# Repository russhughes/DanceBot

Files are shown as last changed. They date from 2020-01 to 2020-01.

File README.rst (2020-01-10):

DanceBot
========

This is my adaptation of the Bobwi DanceBot (https://github.com/G4lile0/Bobwi)
inspired by Zowi (http://diwo.bq.com/en/zowi-cc-by-sa/) and is licesed the same
the originals Attribution-ShareAlike 4.0 International (CC BY-SA 4.0)
http://creativecommons.org/licenses/by-sa/4.0/

|

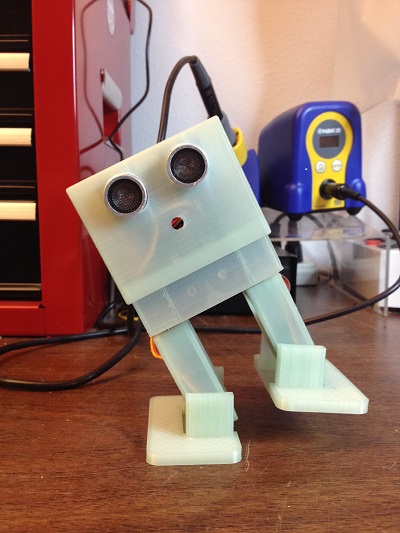
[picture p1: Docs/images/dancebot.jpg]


|

My goal was to simplify assembly for use in Workshops at my local Makerspace
https://confluent.space/. A custom PC board using an Arduino Pro Mini or 
compatible was created to make the electronics assembly easier as well.

|

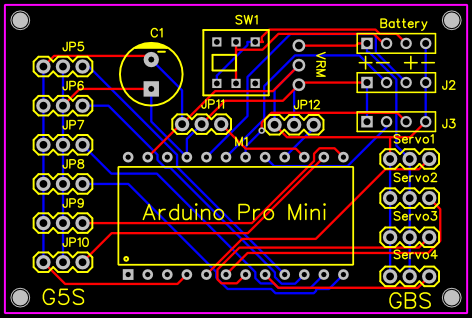
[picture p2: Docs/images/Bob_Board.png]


|

The build instuctions are almost complete but they could use a bit more editing
and a section on calibration.

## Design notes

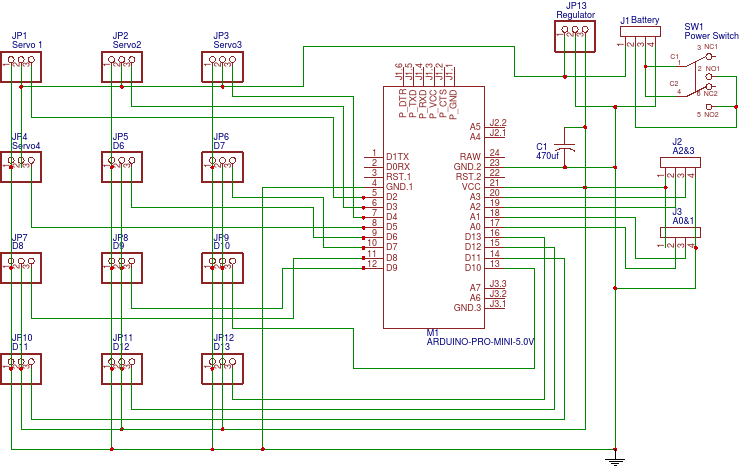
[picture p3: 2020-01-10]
Docs/images/Bob Board Schematic.png

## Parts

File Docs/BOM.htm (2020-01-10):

Dancebot Parts List
1 | 3D Printed parts
1 | Arduino Pro Mini | https://smile.amazon.com/gp/product/B015MGHLNA/
4 | MG90s Servo | https://smile.amazon.com/gp/product/B006VRWV1W/
4 | AA Battery | Almost Anywhere
1 | HC-SR04 | https://smile.amazon.com/gp/product/B00P5W1JLM
1 | 8x8 mm Self-Locking Push Button | https://www.amazon.com/dp/B009750CS4/
2 | 2 x AA 1.5V Battery Holder | https://smile.amazon.com/gp/product/B013GNC08C
1 | CP2102 USB-TTL Board or Similar | https://smile.amazon.com/gp/product/B00SL0U3RG
1 | Pololu #2119 5V Step-up/step-down | https://www.pololu.com/product/2119
1 | DanceBot PCB | https://easyeda.com/EZG0bble/New_Project-Dlf93lfwO
1 | 470uF Electrolytic Capacitor | https://smile.amazon.com/gp/product/B0063C0MPC
2 | 12 Pin Female Header | https://smile.amazon.com/gp/product/B00TGOJE1W
1 | 3 Pin Female Header | "
1 | 6 Pin Male Header | https://smile.amazon.com/gp/product/B00R1LEIL8
2 | 4 Pin Male Header | "
4 | 3 Pin Male Header | "
4 | 2-56 x 3/8" Philips Machine Screw | https://smile.amazon.com/gp/product/B00GX0978W
4 | 2-56 x 1/4" Philips Self Tap Screw | https://smile.amazon.com/gp/product/B00GDZEYOE
4 | 2-56 Hex nut | https://smile.amazon.com/dp/B000H5WW4U
Optional for Easier Calibration
1 | KY-040 Rotary Encoder Module | https://smile.amazon.com/dp/B015QSIRPK
5 | Female to Female Dupont Jumper Wires | https://www.amazon.com/dp/B01M1IEUAF

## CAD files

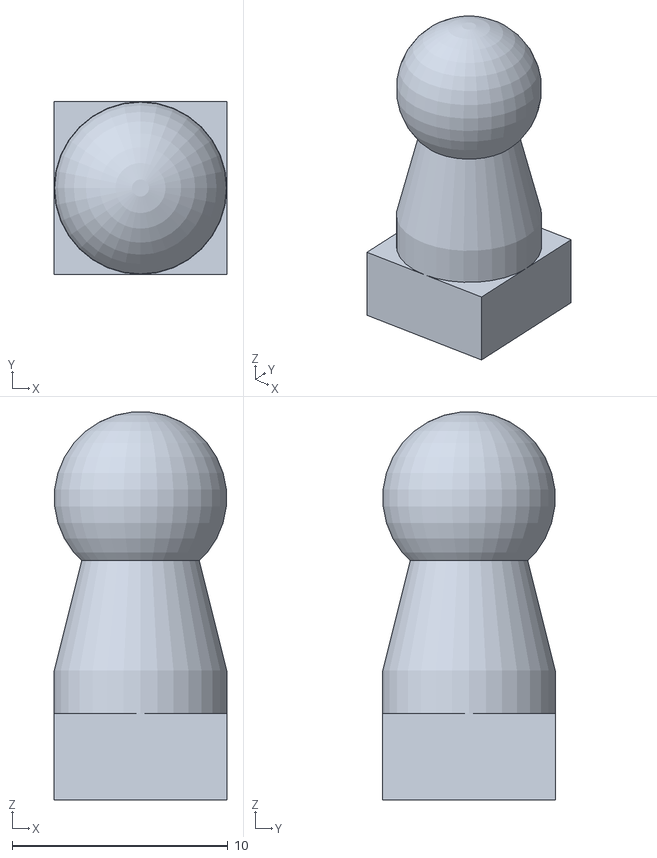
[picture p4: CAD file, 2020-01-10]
3D Printing/BobPowerAntenna.stl
8.00 x 8.00 x 18.0

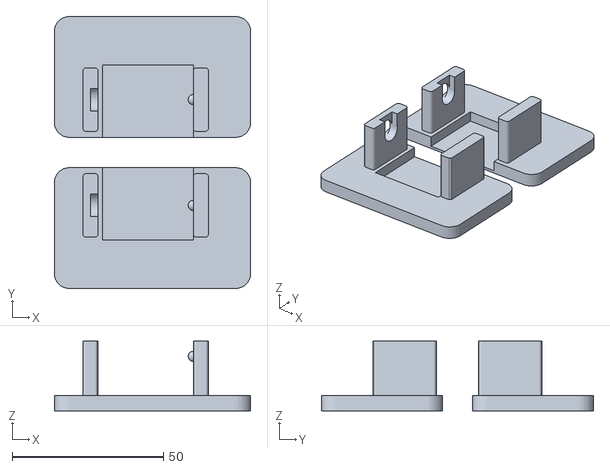
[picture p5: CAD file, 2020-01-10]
3D Printing/BobFeet.stl
65.0 x 90.0 x 23.0

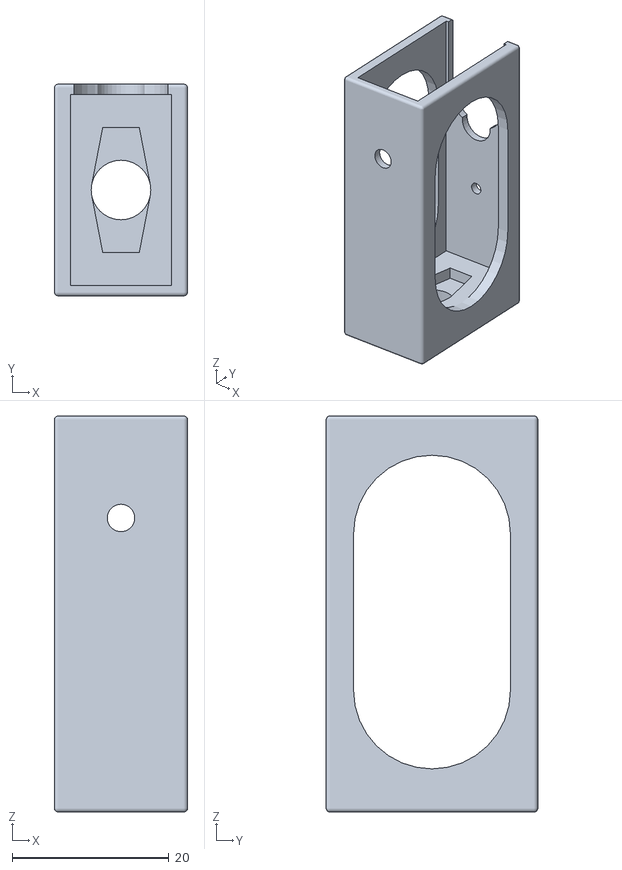
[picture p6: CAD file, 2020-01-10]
3D Printing/BobLeg.stl
17.0 x 27.0 x 50.5

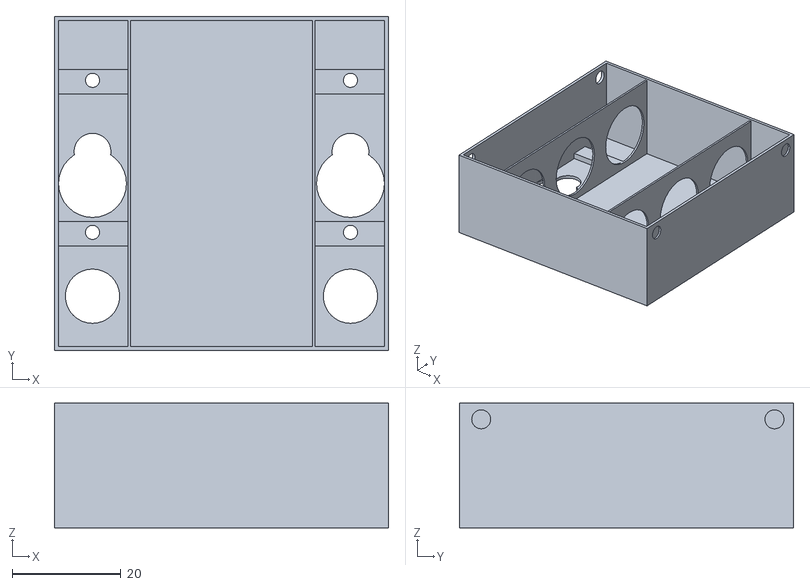
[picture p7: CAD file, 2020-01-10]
3D Printing/BobBase.stl
61.5 x 61.5 x 23.0

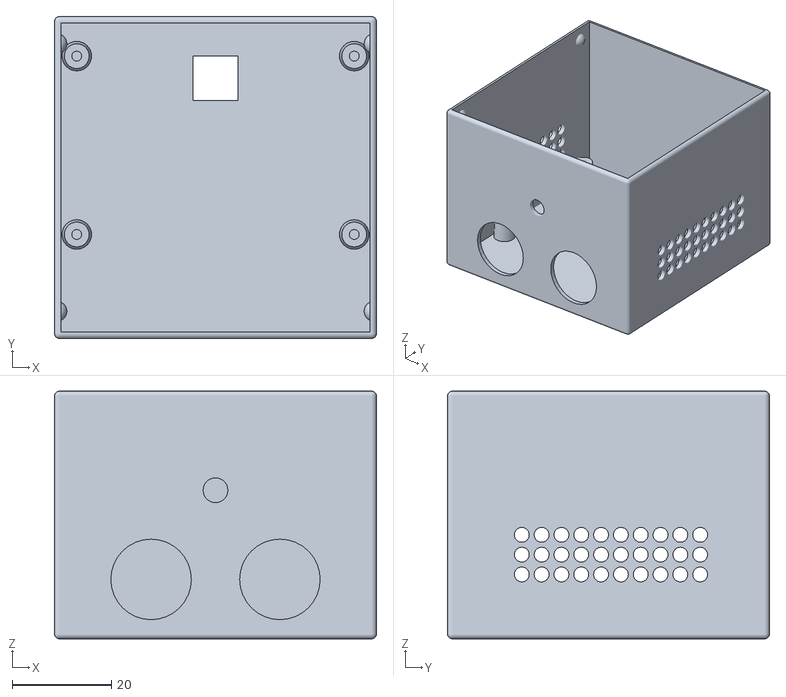
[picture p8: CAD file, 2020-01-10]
3D Printing/BobHead.stl
65.0 x 65.0 x 50.0

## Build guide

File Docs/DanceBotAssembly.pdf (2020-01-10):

# Dance Bot Assembly Instructions

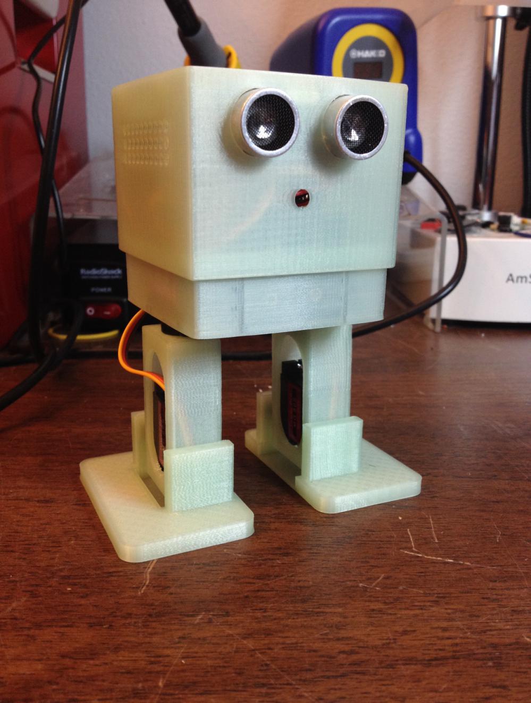
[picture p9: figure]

# 3D Printed Parts

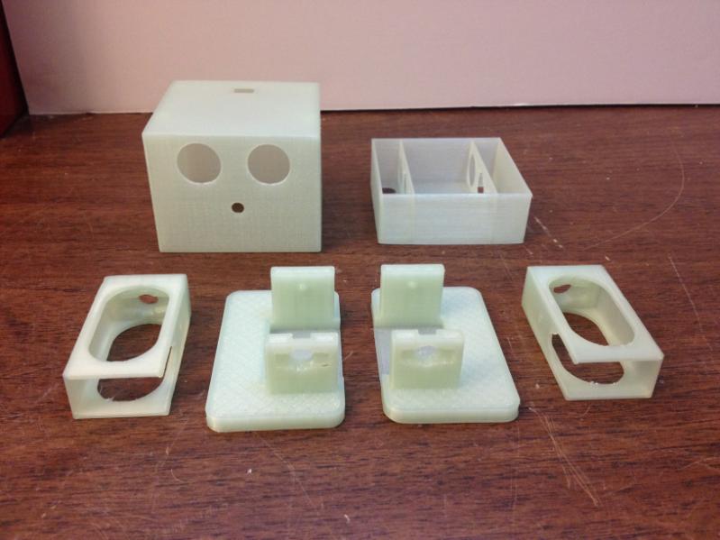
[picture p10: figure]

# Additional Parts

# PC Board Assembly

[_] Insert a four pin male header in J2 & J3.

[_] Insert a three pin male header in to Servo1, Servo2, Servo3 and Servo4.

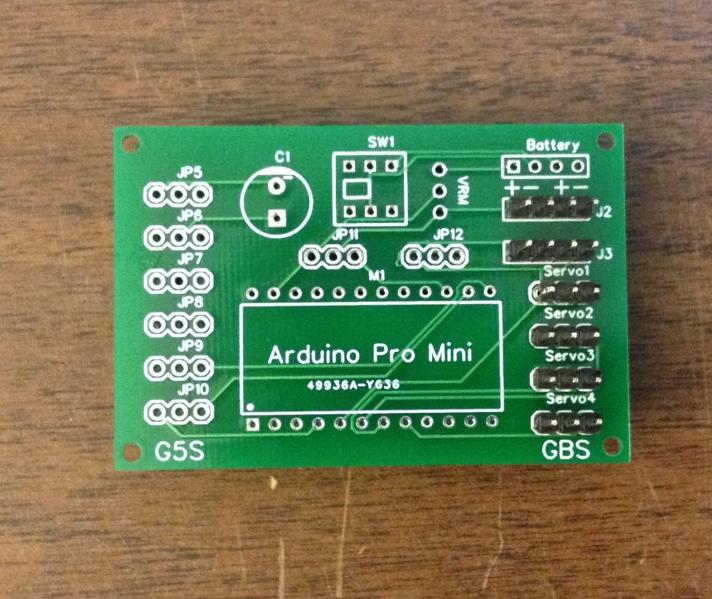
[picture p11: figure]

You can use one of the 12 pin female headers to help hold the male headers in place.

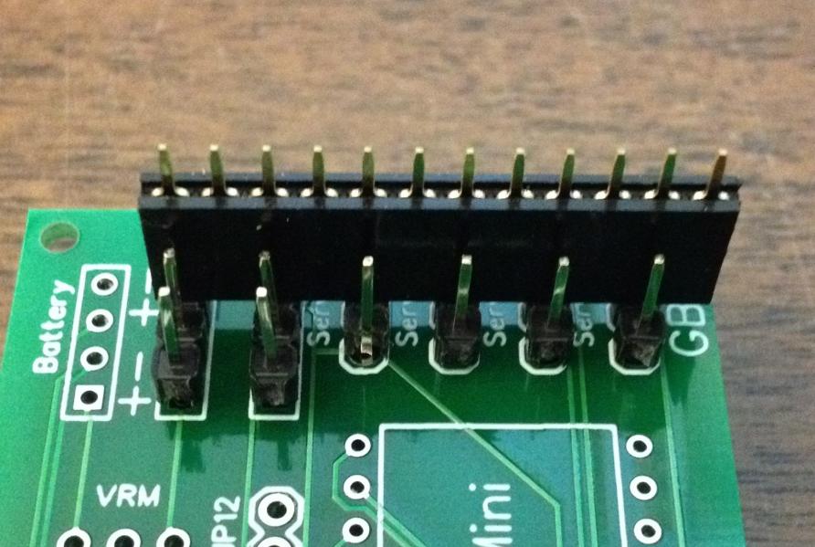
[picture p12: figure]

[_] solder the pins on the other side of the PCB.

[_] Insert the three pin female header into VRM and solder.

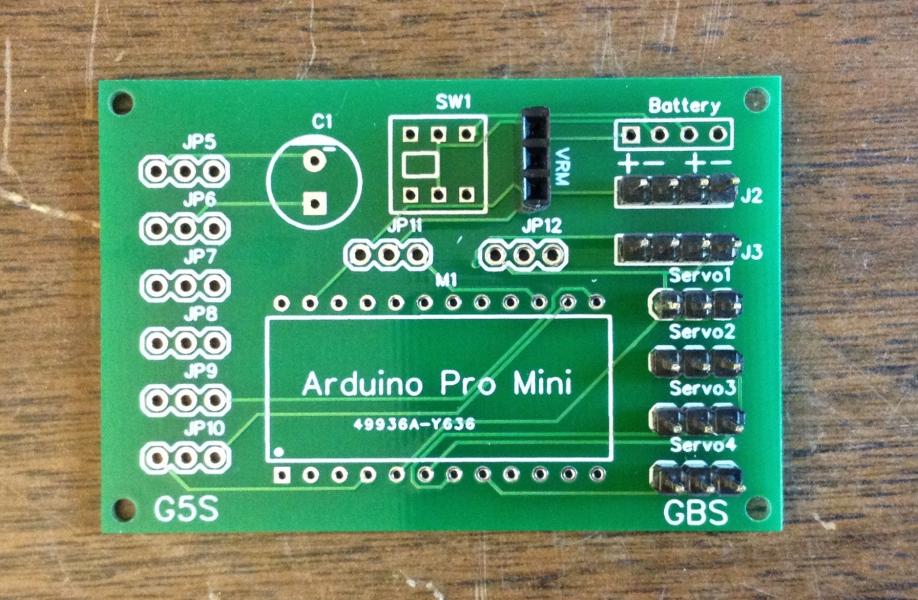
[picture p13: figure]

[_] Insert the two 12 pin female headers for the Arduino Pro Mini and solder. You can use one of the 12 pin male headers across the 12 pin female headers and the 3 pin VRM female header to help hold them in place while you solder them.

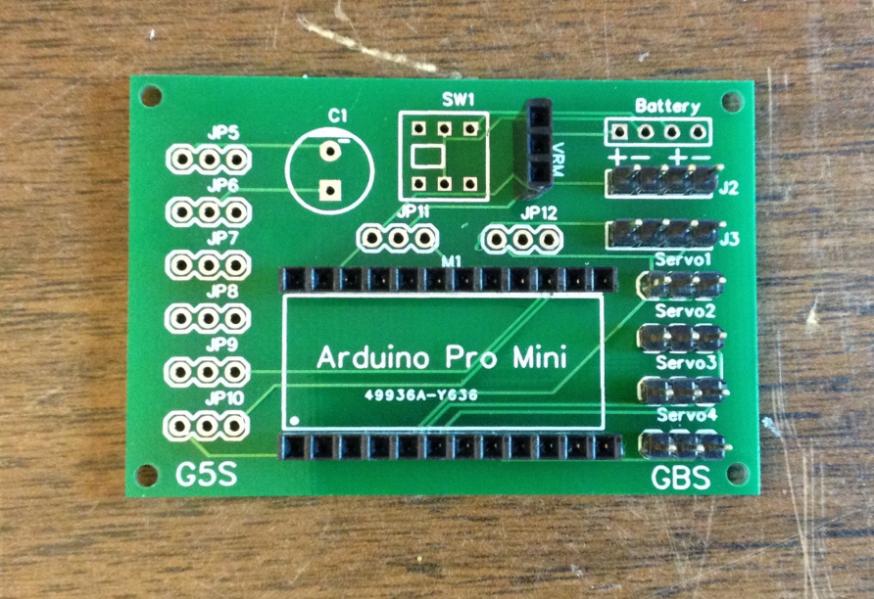
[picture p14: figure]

[_] Insert the 470uf electrolytic capacitor in C1 being careful to make sure the negative pin of the capacitor is inserted into the upper hole on the PC Board that is identified with the “-“ symbol.

[_] Insert the two 12 pin male headers into the two 12 pin female headers as show below

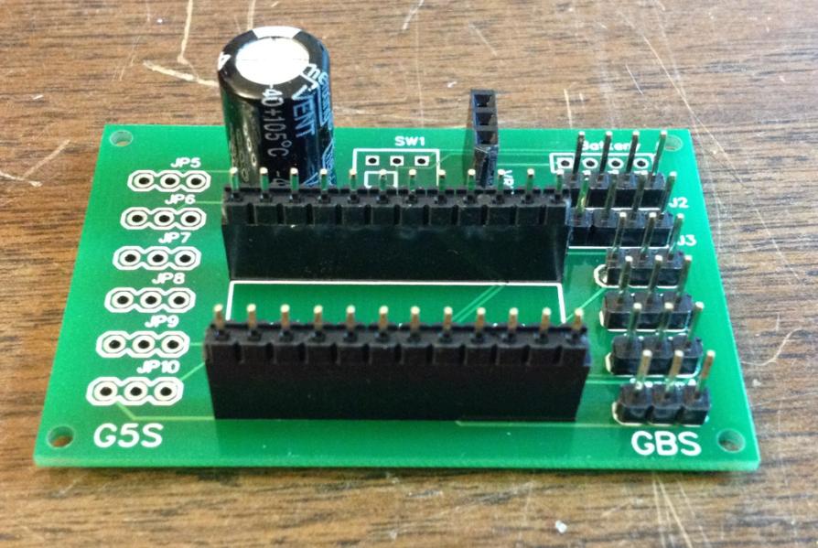
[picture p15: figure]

[_] Place the Arduino Pro Mini on the two 12 pin male headers being careful it is orientated as show in the picture below. Solder each of the pins to the Arduino.

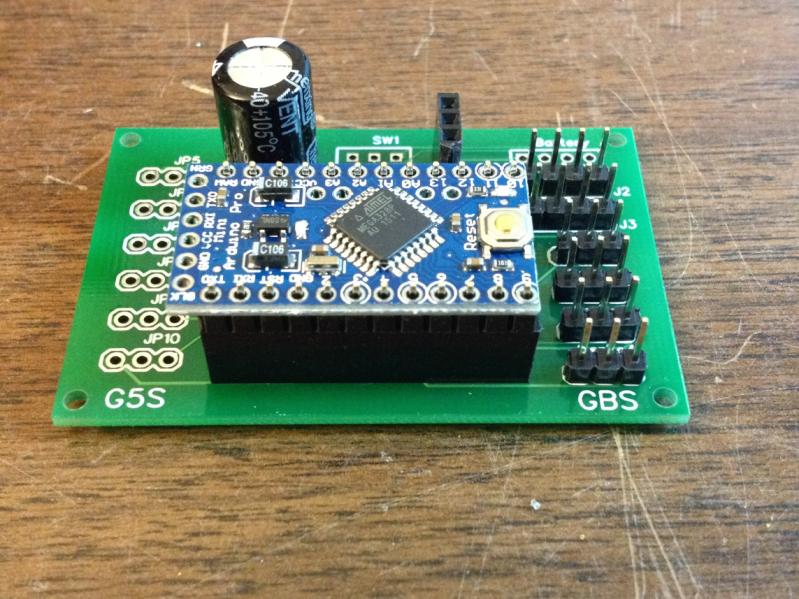
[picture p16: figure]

At this point your PC board should like the one pictured below.

[_] Turn the PC Board over and insert the locking power button into the SW1 position. Be sure the power button is on the opposite side of the PC board from the other components. Solder it in place.

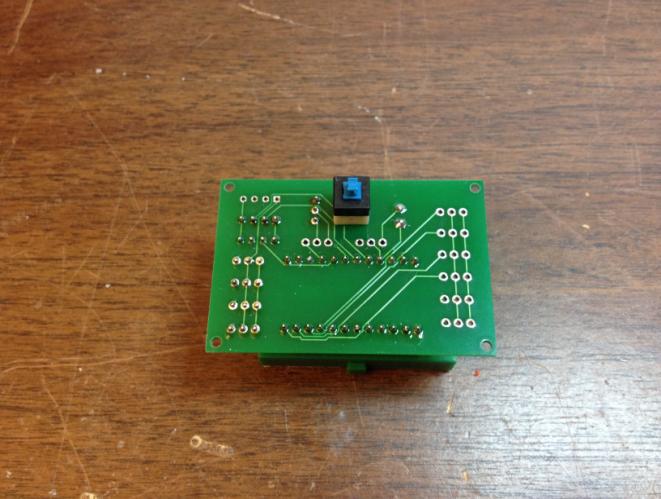
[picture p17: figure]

[_] Insert the Red wire from the first AA battery holder into first hole of the Battery port labeled with a ‘+’ symbol and solder.

[_] Insert the Black wire from the first AA battery holder into the second hold of the Battery port labeled with a ‘=’ symbol and solder.

[_] Insert the Red wire from the second AA battery holder into the third hole of the Battery port labeled with a ‘+’ symbol and solder.

[_] Insert the Black wire from the second AA battery holder into the fourth hole of the Battery port labeled with a ‘_’ symbol and solder.

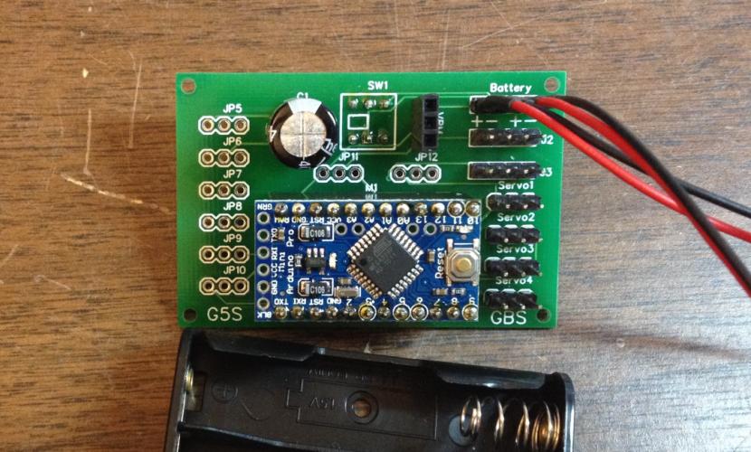
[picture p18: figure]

[_] Remove the Arduino Pro Mini from the PC Board by gently wiggling it while pulling on it.

[_] insert the six pin male header into the programming port of the Arduino Pro Mini and solder.

[_] Insert the 3 pin right angle male header into the Voltage Regulation Module and solder.

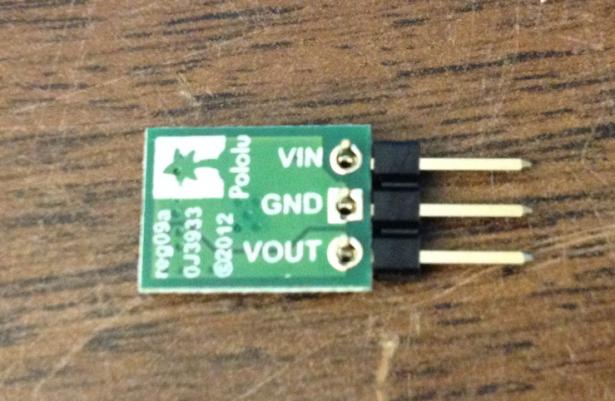
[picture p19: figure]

[_] Replace the Arduino Pro Mini back onto the PC Board being careful that programming port is to the left side of the PC Board.

[_] Insert the Voltage Regulation Module into the VRM port with the back side of the board marked with VOUT, GND and VIN facing the Battery port as shown in the picture below.

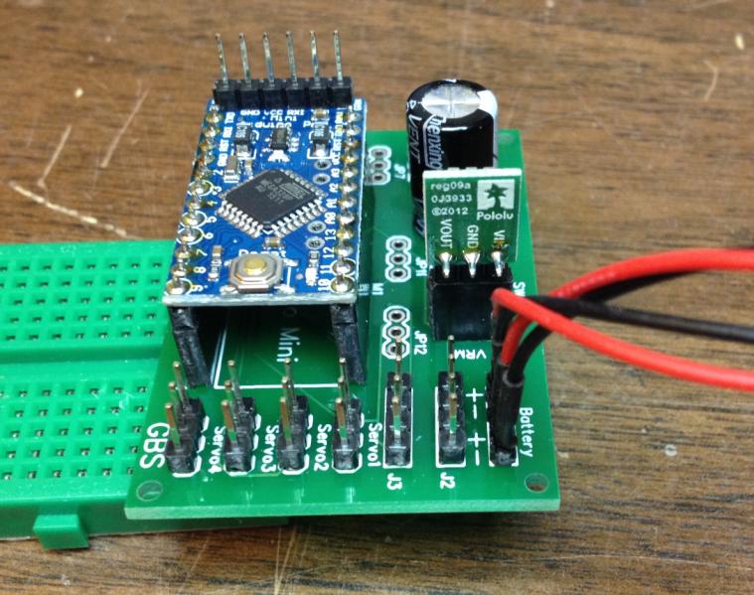
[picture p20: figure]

[_] Trim each of the four servo horns so they have two holes on each side of the hub.

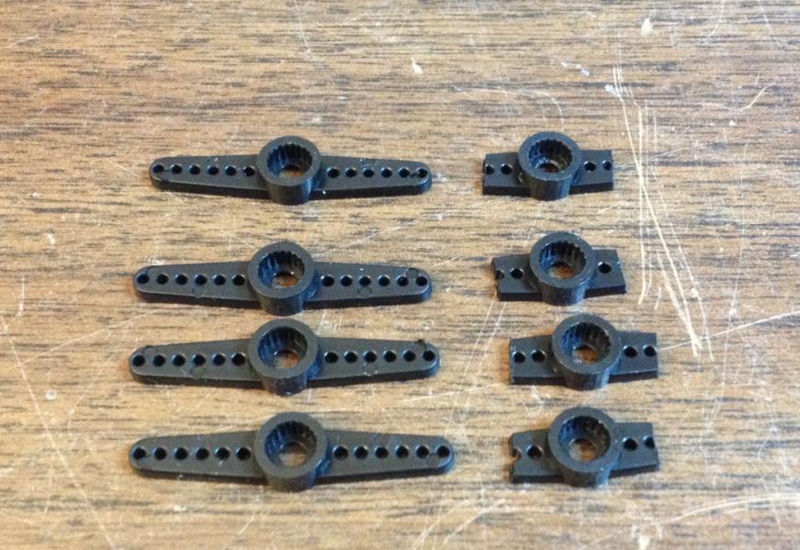
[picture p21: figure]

[_] Insert one of the trimmed servo horns into each of the 3D printed legs as shown below. They are a press fit so use a screwdriver to make sure the servo horn is fully inserted into the leg.

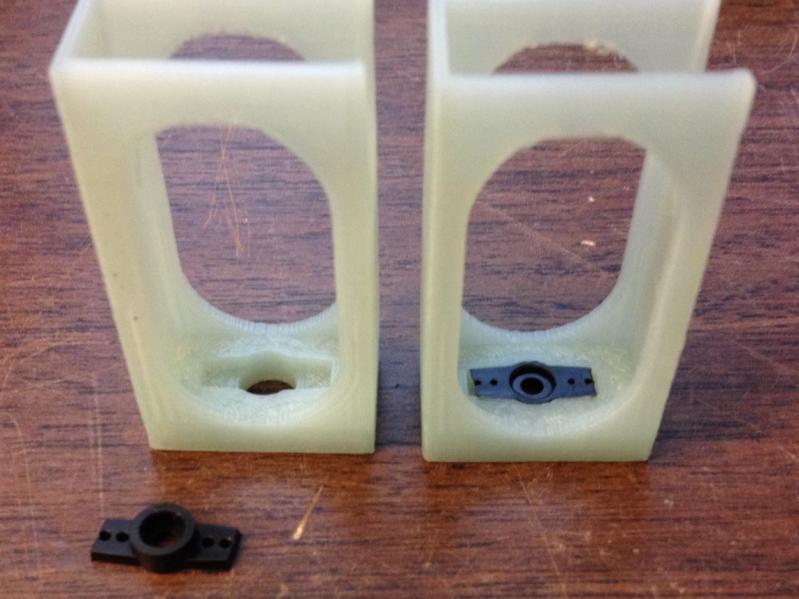
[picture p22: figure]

[_] Insert two of the servos into the 3D printed Base and secure with 2 M2 screws and nuts.

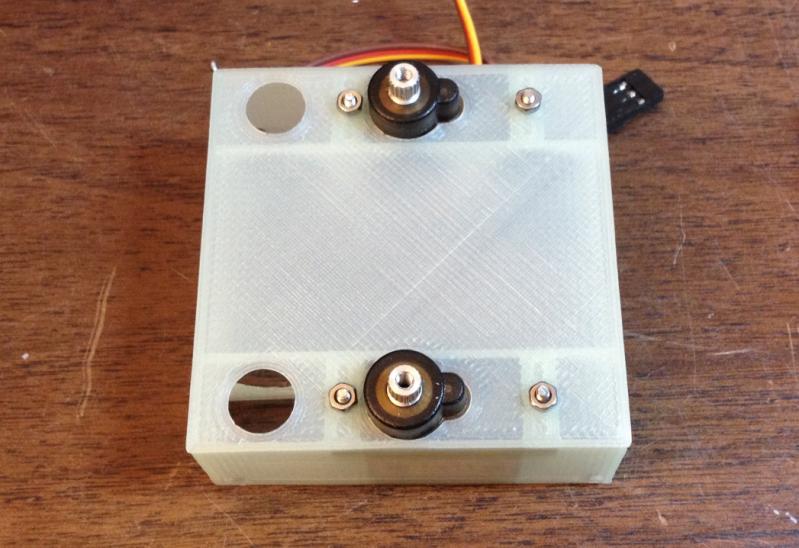
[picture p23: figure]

[_] Use 4 2-56 x ¼” self tapping screws to mount the PC Board inside the 3D printed Head. The shaft of the locking power button should be sticking through the square hole in the top of the head.

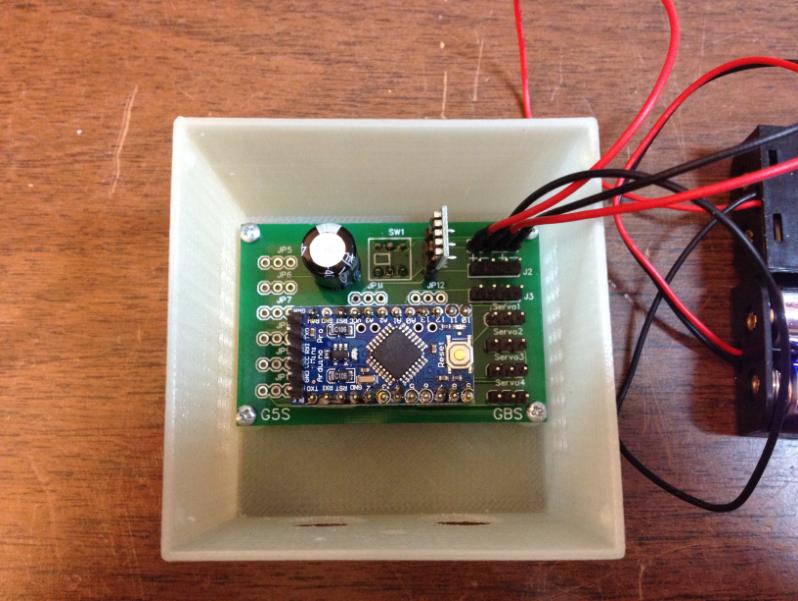
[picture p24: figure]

[_] Press fit the Legs to the servos mounted in the base. The legs should be as “square” as possible with the base before securing them using the small machine screw provided with the servos. Hold the legs still so the servo doesn’t rotate as you tighten the screw. It might not be possible to get the legs perfectly “square” and some misalignment of the Legs can be corrected for during “calibration.”

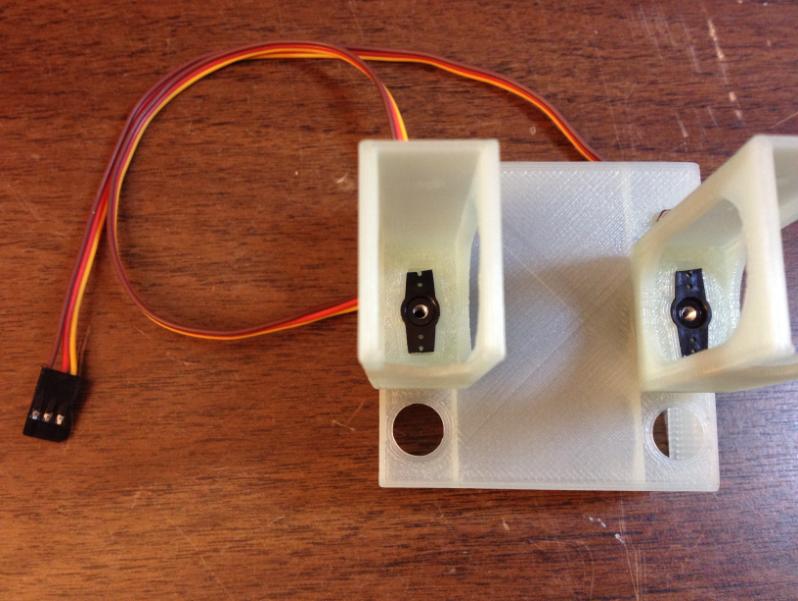
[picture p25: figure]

[_] Insert one of the remaining servos into each Leg as shown below. Dress the servos cable down behind the servo and out the side of the leg and through the small hole in the bottom of the base. Affix the servos in place using one of the small sheet metal screws provided with the servos.\

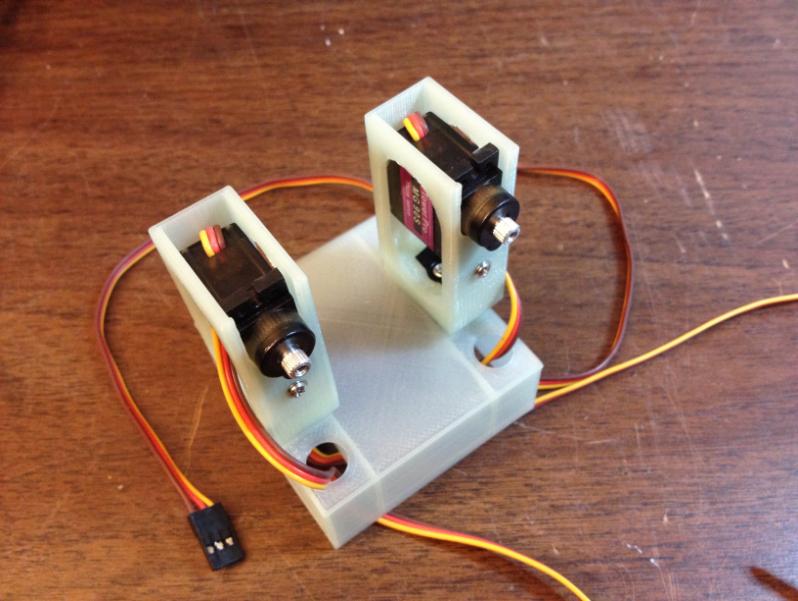
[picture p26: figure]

[_] Lay the bot on its side and attach the right foot to the right leg as shown below. Align the bump on the front of the foot with hole in the front of the leg and slide the servo horn through the cutout in the back of the foot. It is a tight fit so you may need to flex the foot a little to get it to fit. Be careful not to rotate the servo’s shaft while you are attaching the foot.

[_] Attach the left foot to the left leg using the same procedure as the other leg.

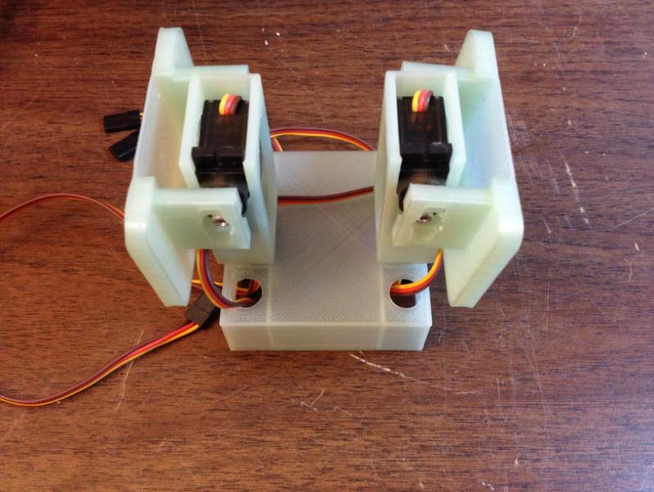
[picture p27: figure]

[_] Stand the bot up with its feet flat on the table and press one of the two remaining trimmed servo horns onto the servo’s shaft. Secure the servo horn using the small machine screw provided with the servo being careful not to rotate the servo’s shaft.

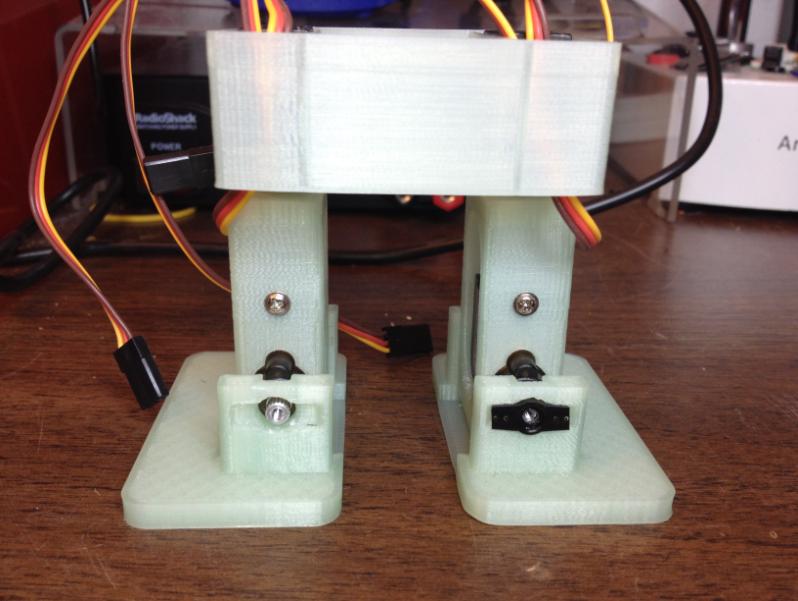
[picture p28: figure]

[_] Connect the four servo cables to the Servo1, Servo2, Servo3 and Servo4 ports. The brown wires (ground) should be on the left and the yellow wire (signal) to the right.

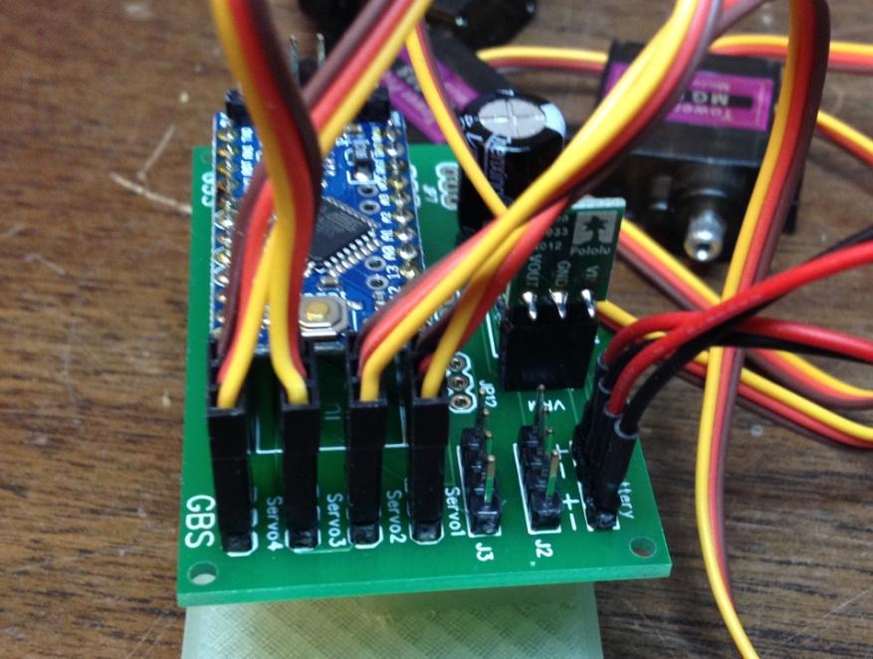
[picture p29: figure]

With the Bot standing up and facing you:

- The top left servo connects to Servo1
- The top right servo connects to Servo2
- The bottom left servo connects to Servo3
- The bottom right servo connects to Servo4

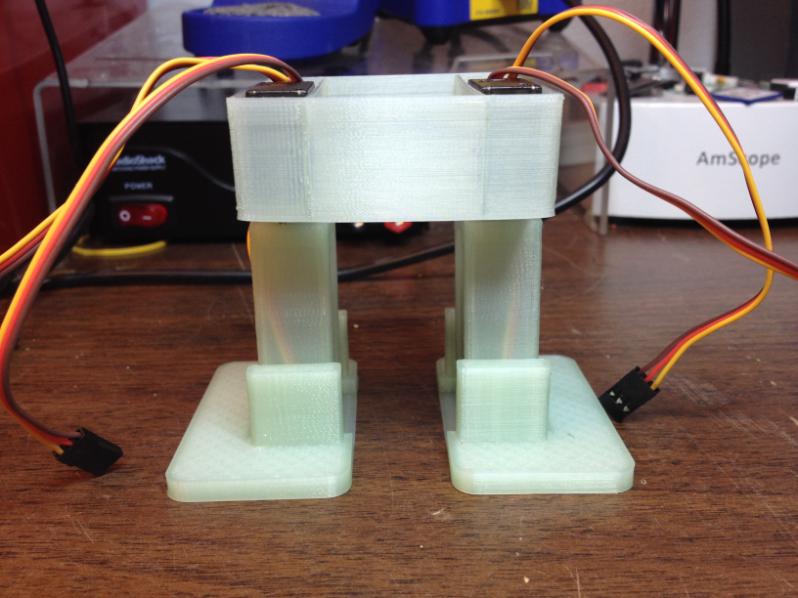
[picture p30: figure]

[_] Place the two battery holders into the base as shown below.

[_] Attach the calibration tool to the PC Board. The connector with 2 wires connects to the J2 port and the connector with the 3 wire connects to the J3 port.

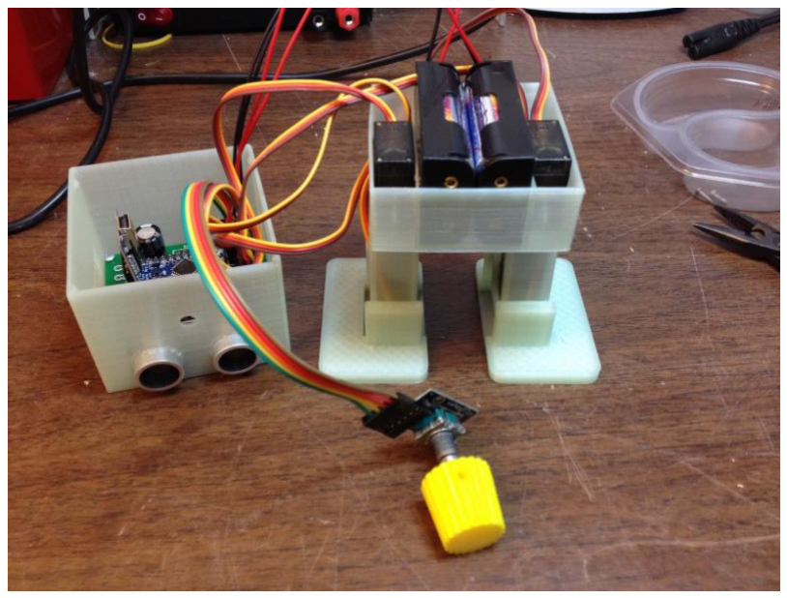
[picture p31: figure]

[_]

[_]

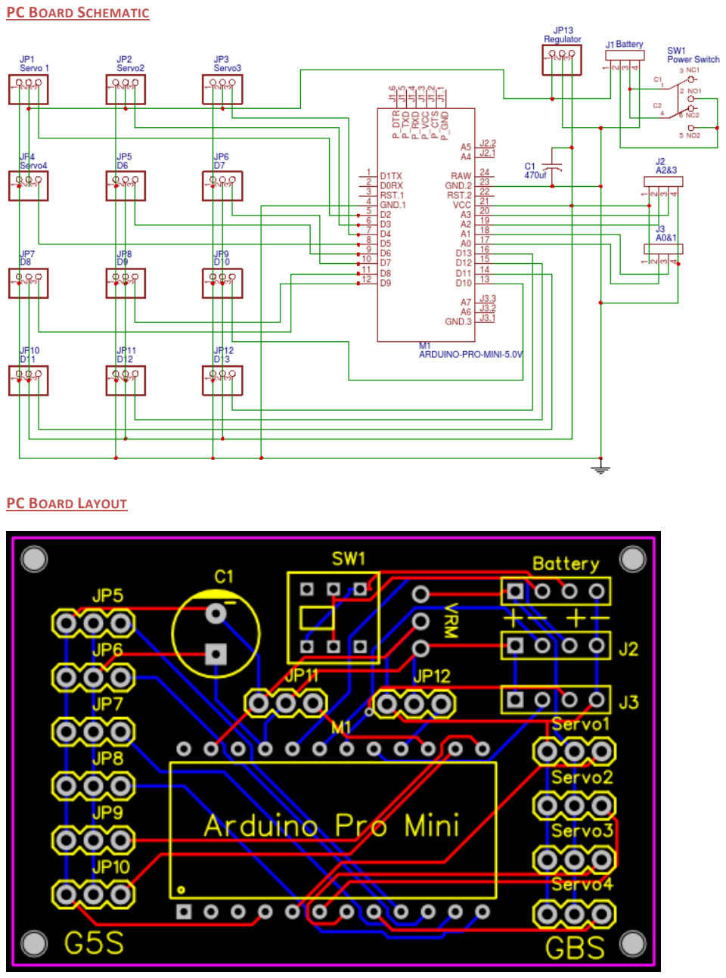
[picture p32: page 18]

PC BOARD SCHEMATIC

PC BOARD LAYOUT

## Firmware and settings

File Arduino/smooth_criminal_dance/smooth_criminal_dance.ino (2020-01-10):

//
// smooth_criminal_dance.ino
//
// From the zowi repo https://github.com/bq/zowi
// https://github.com/bq/zowi/blob/master/Zowi_3Dprintable/code/zum/smooth_criminal/smooth_criminal.ino
// Attribution-ShareAlike 4.0 International (CC BY-SA 4.0)
//
// Lightly modified to work with my hardware as used in my Confluent Makespace Class
//

#include <Servo.h>
#include <Oscillator.h>
#include <EEPROM.h>

#define N_SERVOS 4

#define EEPROM_TRIM false //Activar para coger los datos de calibracin desde la memoria interna

//  zowi.setTrims(3,3,0,5);

#define TRIM_YR -7
#define TRIM_YL -7
#define TRIM_RR -8
#define TRIM_RL 1


/* orig
#define PIN_RR 9
#define PIN_RL 7
#define PIN_YR 8
#define PIN_YL 6
*/

/* bob board version */


#define PIN_YR 2
#define PIN_YL 3
#define PIN_RR 4
#define PIN_RL 5

#define INTERVALTIME 10.0
int freeze = 0;
int	dist = 0;
Oscillator servo[N_SERVOS];

void goingUp(int tempo);
void drunk (int tempo);
void noGravity(int tempo);
void kickLeft(int tempo);
void kickRight(int tempo);
void run(int steps, int T=500);
void walk(int steps, int T=1000);
void backyard(int steps, int T=3000);
void backyardSlow(int steps, int T=5000);
void turnLeft(int steps, int T=3000);
void turnRight(int steps, int T=3000);
void moonWalkLeft(int steps, int T=1000);
void moonWalkRight(int steps, int T=1000);
void crusaito(int steps, int T=1000);
void swing(int steps, int T=1000);
void upDown(int steps, int T=1000);
void flapping(int steps, int T=1000);

void setup()
{
	Serial.begin(9600);
	Serial.println("Running..");
  	servo[0].attach(PIN_RR);
  	servo[1].attach(PIN_RL);
  	servo[2].attach(PIN_YR);
  	servo[3].attach(PIN_YL);

    servo[0].SetTrim(TRIM_RR);
    servo[1].SetTrim(TRIM_RL);
    servo[2].SetTrim(TRIM_YR);
    servo[3].SetTrim(TRIM_YL);
    for(int i=0;i<4;i++) servo[i].SetPosition(90);

}

// TEMPO: 121 BPM
int t=495;
double pause=0;

void loop()
{
	dance();
	for(int i=0;i<4;i++) servo[i].SetPosition(90);
 	while(1) ;
}

void dance(){
  primera_parte();
  segunda_parte();
  moonWalkLeft(4,t*2);
  moonWalkRight(4,t*2);
  moonWalkLeft(4,t*2);
  moonWalkRight(4,t*2);
  primera_parte();
  crusaito(1,t*8);
  crusaito(1,t*7);

  for (int i=0; i<16; i++){
    flapping(1,t/4);
    delay(3*t/4);
  }

  moonWalkRight(4,t*2);
  moonWalkLeft(4,t*2);
  moonWalkRight(4,t*2);
  moonWalkLeft(4,t*2);

  drunk(t*4);
  drunk(t*4);
  drunk(t*4);
  drunk(t*4);
  kickLeft(t);
  kickRight(t);
  drunk(t*8);
  drunk(t*4);
  drunk(t/2);
  delay(t*4);

  drunk(t/2);

  delay(t*4);
  walk(2,t*2);
  backyard(2,t*2);
  goingUp(t*2);
  goingUp(t*1);
  noGravity(t*2);
  crusaito(1,t*2);
  crusaito(1,t*8);
  crusaito(1,t*2);
  crusaito(1,t*8);
  crusaito(1,t*2);
  crusaito(1,t*3);

  delay(t);
  primera_parte();
    for (int i=0; i<32; i++){
    flapping(1,t/2);
    delay(t/2);
  }

  for(int i=0;i<4;i++) servo[i].SetPosition(90);
}

////////////////////////////////////////////////////////////////////////////////////////
//////////////////////////////////FUNCIONES DE CONTROL//////////////////////////////////
////////////////////////////////////////////////////////////////////////////////////////

void oscillate(int A[N_SERVOS], int O[N_SERVOS], int T, double phase_diff[N_SERVOS]){

  for (int i=0; i<4; i++) {
    servo[i].SetO(O[i]);
    servo[i].SetA(A[i]);
    servo[i].SetT(T);
    servo[i].SetPh(phase_diff[i]);
  }
  double ref=millis();
   for (double x=ref; x<T+ref; x=millis()){
     for (int i=0; i<4; i++){
        servo[i].refresh();
     }
  }
}

unsigned long final_time;
unsigned long interval_time;
int oneTime;
int iteration;
float increment[N_SERVOS];
int oldPosition[]={90,90,90,90};

void moveNServos(int time, int  newPosition[]){
  for(int i=0;i<N_SERVOS;i++)	increment[i] = ((newPosition[i])-oldPosition[i])/(time/INTERVALTIME);

  final_time =  millis() + time;

  iteration = 1;
  while(millis() < final_time){ //Javi del futuro cambia esto
      interval_time = millis()+INTERVALTIME;

      oneTime=0;
      while(millis()<interval_time){
          if(oneTime<1){
              for(int i=0;i<N_SERVOS;i++){
                  servo[i].SetPosition(oldPosition[i] + (iteration * increment[i]));
              }
              iteration++;
              oneTime++;
          }
      }
  }

  for(int i=0;i<N_SERVOS;i++){
    oldPosition[i] = newPosition[i];
  }
}

//////////////////////////////////////////////////////////////////////////////
////////////////////////////////PASOS DE BAILE////////////////////////////////
//////////////////////////////////////////////////////////////////////////////

void goingUp(int tempo){

      pause=millis();
      for(int i=0;i<4;i++) servo[i].SetPosition(90);
      delay(tempo);
      servo[0].SetPosition(80);
      servo[1].SetPosition(100);
      delay(tempo);
      servo[0].SetPosition(70);
      servo[1].SetPosition(110);
      delay(tempo);
      servo[0].SetPosition(60);
      servo[1].SetPosition(120);
      delay(tempo);
      servo[0].SetPosition(50);
      servo[1].SetPosition(130);
      delay(tempo);
      servo[0].SetPosition(40);
      servo[1].SetPosition(140);
      delay(tempo);
      //servo[0].SetPosition(30);
      //servo[1].SetPosition(150);
      delay(tempo);
      //servo[0].SetPosition(20);
      //servo[1].SetPosition(160);
      delay(tempo);

      while(millis()<pause+8*t);

}

void primera_parte(){

  int move1[4] = {60,120,90,90};
  int move2[4] = {90,90,90,90};
  int move3[4] = {40,140,90,90};

  for(int x=0; x<3; x++){
    for(int i=0; i<3; i++){
      lateral_fuerte(1,t/2);
      lateral_fuerte(0,t/4);
      lateral_fuerte(1,t/4);
      delay(t);
    }

    pause=millis();
    for(int i=0;i<4;i++) servo[i].SetPosition(90);
    moveNServos(t*0.4,move1);
    moveNServos(t*0.4,move2);
    while(millis()<(pause+t*2));
  }

  for(int i=0; i<2; i++){
    lateral_fuerte(1,t/2);
    lateral_fuerte(0,t/4);
    lateral_fuerte(1,t/4);
    delay(t);
  }

  pause=millis();
  for(int i=0;i<4;i++) servo[i].SetPosition(90);
  crusaito(1,t*1.4);
  moveNServos(t*1,move3);
  for(int i=0;i<4;i++) servo[i].SetPosition(90);
  while(millis()<(pause+t*4));
}

void segunda_parte(){

  int move1[4] = {90,90,80,100};
  int move2[4] = {90,90,100,80};
  int move3[4] = {90,90,80,100};
  int move4[4] = {90,90,100,80};

  int move5[4] = {40,140,80,100};
  int move6[4] = {40,140,100,80};
  int move7[4] = {90,90,80,100};
  int move8[4] = {90,90,100,80};

  int move9[4] = {40,140,80,100};
  int move10[4] = {40,140,100,80};
  int move11[4] = {90,90,80,100};
  int move12[4] = {90,90,100,80};

  for(int x=0; x<7; x++){
    for(int i=0; i<3; i++){
      pause=millis();
      moveNServos(t*0.15,move1);
      moveNServos(t*0.15,move2);
      moveNServos(t*0.15,move3);
      moveNServos(t*0.15,move4);
      while(millis()<(pause+t));
    }
    pause=millis();
    moveNServos(t*0.15,move5);
    moveNServos(t*0.15,move6);
    moveNServos(t*0.15,move7);
    moveNServos(t*0.15,move8);
    while(millis()<(pause+t));
  }

  for(int i=0; i<3; i++){
    pause=millis();
    moveNServos(t*0.15,move9);
    moveNServos(t*0.15,move10);
    moveNServos(t*0.15,move11);
    moveNServos(t*0.15,move12);
    while(millis()<(pause+t));
  }
}

void lateral_fuerte(boolean side, int tempo){

  for(int i=0;i<4;i++) servo[i].SetPosition(90);
  if (side) servo[0].SetPosition(40);
  else servo[1].SetPosition(140);
  delay(tempo/2);
  servo[0].SetPosition(90);
  servo[1].SetPosition(90);
  delay(tempo/2);

}

void drunk (int tempo){

  pause=millis();

  int move1[] = {60,70,90,90};
  int move2[] = {110,120,90,90};
  int move3[] = {60,70,90,90};
  int move4[] = {110,120,90,90};

  moveNServos(tempo*0.235,move1);
  moveNServos(tempo*0.235,move2);
  moveNServos(tempo*0.235,move3);
  moveNServos(tempo*0.235,move4);
  while(millis()<(pause+tempo));

}


void noGravity(int tempo){

  int move1[4] = {100,120,90,90};
  int move2[4] = {120,120,90,90};
  int move3[4] = {100,120,90,90};
  int move4[4] = {90,90,90,90};


  for(int i=0;i<4;i++) servo[i].SetPosition(90);
  for(int i=0;i<N_SERVOS;i++) oldPosition[i]=90;
  moveNServos(tempo*2,move1);
  moveNServos(tempo*2,move2);
  delay(tempo*2);
  moveNServos(tempo*2,move3);
  moveNServos(tempo*2,move4);



}

void kickLeft(int tempo){
  for(int i=0;i<4;i++) servo[i].SetPosition(90);
  delay(tempo);
  servo[0].SetPosition(50); //pie derecho
  servo[1].SetPosition(70); //pie izquiero
  delay(tempo);
  servo[0].SetPosition(80); //pie derecho
  servo[1].SetPosition(70); //pie izquiero
  delay(tempo/4);
  servo[0].SetPosition(30); //pie derecho
  servo[1].SetPosition(70); //pie izquiero
  delay(tempo/4);
  servo[0].SetPosition(80); //pie derecho
  servo[1].SetPosition(70); //pie izquiero
  delay(tempo/4);
  servo[0].SetPosition(30); //pie derecho
  servo[1].SetPosition(70); //pie izquiero
  delay(tempo/4);
  servo[0].SetPosition(80); //pie derecho
  servo[1].SetPosition(70); //pie izquiero
  delay(tempo);
}

void kickRight(int tempo){
for(int i=0;i<4;i++) servo[i].SetPosition(90);
  delay(tempo);
  servo[0].SetPosition(110); //pie derecho
  servo[1].SetPosition(130); //pie izquiero
  delay(tempo);
  servo[0].SetPosition(110); //pie derecho
  servo[1].SetPosition(100); //pie izquiero
  delay(tempo/4);
  servo[0].SetPosition(110); //pie derecho
  servo[1].SetPosition(150); //pie izquiero
  delay(tempo/4);
  servo[0].SetPosition(110); //pie derecho
  servo[1].SetPosition(80); //pie izquiero
  delay(tempo/4);
  servo[0].SetPosition(110); //pie derecho
  servo[1].SetPosition(150); //pie izquiero
  delay(tempo/4);
  servo[0].SetPosition(110); //pie derecho
  servo[1].SetPosition(100); //pie izquiero
  delay(tempo);
}

void walk(int steps, int T){
    int A[4]= {15, 15, 30, 30};
    int O[4] = {0, 0, 0, 0};
    double phase_diff[4] = {DEG2RAD(0), DEG2RAD(0), DEG2RAD(90), DEG2RAD(90)};

    for(int i=0;i<steps;i++)oscillate(A,O, T, phase_diff);
}

void run(int steps, int T){
    int A[4]= {10, 10, 10, 10};
    int O[4] = {0, 0, 0, 0};
    double phase_diff[4] = {DEG2RAD(0), DEG2RAD(0), DEG2RAD(90), DEG2RAD(90)};

    for(int i=0;i<steps;i++)oscillate(A,O, T, phase_diff);
}

void backyard(int steps, int T){
    int A[4]= {15, 15, 30, 30};
    int O[4] = {0, 0, 0, 0};
    double phase_diff[4] = {DEG2RAD(0), DEG2RAD(0), DEG2RAD(-90), DEG2RAD(-90)};

    for(int i=0;i<steps;i++)oscillate(A,O, T, phase_diff);
}

void backyardSlow(int steps, int T){
    int A[4]= {15, 15, 30, 30};
    int O[4] = {0, 0, 0, 0};
    double phase_diff[4] = {DEG2RAD(0), DEG2RAD(0), DEG2RAD(-90), DEG2RAD(-90)};

    for(int i=0;i<steps;i++)oscillate(A,O, T, phase_diff);
}


void turnLeft(int steps, int T){
    int A[4]= {20, 20, 10, 30};
    int O[4] = {0, 0, 0, 0};
    double phase_diff[4] = {DEG2RAD(0), DEG2RAD(0), DEG2RAD(90), DEG2RAD(90)};

    for(int i=0;i<steps;i++)oscillate(A,O, T, phase_diff);
}

void turnRight(int steps, int T){
    int A[4]= {20, 20, 30, 10};
    int O[4] = {0, 0, 0, 0};
    double phase_diff[4] = {DEG2RAD(0), DEG2RAD(0), DEG2RAD(90), DEG2RAD(90)};

    for(int i=0;i<steps;i++)oscillate(A,O, T, phase_diff);
}

void moonWalkRight(int steps, int T){
    int A[4]= {25, 25, 0, 0};
    int O[4] = {-15 ,15, 0, 0};
    double phase_diff[4] = {DEG2RAD(0), DEG2RAD(180 + 120), DEG2RAD(90), DEG2RAD(90)};

    for(int i=0;i<steps;i++)oscillate(A,O, T, phase_diff);
}

void moonWalkLeft(int steps, int T){
    int A[4]= {25, 25, 0, 0};
    int O[4] = {-15, 15, 0, 0};
    double phase_diff[4] = {DEG2RAD(0), DEG2RAD(180 - 120), DEG2RAD(90), DEG2RAD(90)};

    for(int i=0;i<steps;i++)oscillate(A,O, T, phase_diff);
}

void crusaito(int steps, int T){
    int A[4]= {25, 25, 30, 30};
    int O[4] = {- 15, 15, 0, 0};
    double phase_diff[4] = {DEG2RAD(0), DEG2RAD(180 + 120), DEG2RAD(90), DEG2RAD(90)};

    for(int i=0;i<steps;i++)oscillate(A,O, T, phase_diff);
}

void swing(int steps, int T){
    int A[4]= {25, 25, 0, 0};
    int O[4] = {-15, 15, 0, 0};
    double phase_diff[4] = {DEG2RAD(0), DEG2RAD(0), DEG2RAD(90), DEG2RAD(90)};

    for(int i=0;i<steps;i++)oscillate(A,O, T, phase_diff);
}

void upDown(int steps, int T){
    int A[4]= {25, 25, 0, 0};
    int O[4] = {-15, 15, 0, 0};
    double phase_diff[4] = {DEG2RAD(180), DEG2RAD(0), DEG2RAD(270), DEG2RAD(270)};

    for(int i=0;i<steps;i++)oscillate(A,O, T, phase_diff);
}

void flapping(int steps, int T){
    int A[4]= {15, 15, 8, 8};
    int O[4] = {-A[0], A[1], 0, 0};
    double phase_diff[4] = {DEG2RAD(0), DEG2RAD(180), DEG2RAD(90), DEG2RAD(-90)};

    for(int i=0;i<steps;i++)oscillate(A,O, T, phase_diff);
}

void test(int steps, int T){
    int A[4]= {15, 15, 8, 8};
    int O[4] = {-A[0] + 10, A[1] - 10, 0, 0};
    double phase_diff[4] = {DEG2RAD(0), DEG2RAD(180), DEG2RAD(90), DEG2RAD(-90)};

    for(int i=0;i<steps;i++)oscillate(A,O, T, phase_diff);
}

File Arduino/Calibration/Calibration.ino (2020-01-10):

 /* Read Quadrature Encoder
  * Connect Encoder to Pins encoder0PinA, encoder0PinB, and +5V.
  *
  * Sketch by max wolf / www.meso.net
  * v. 0.1 - very basic functions - mw 20061220
  *
  */  

#include <Servo.h>
#include <Oscillator.h> //Librera ArduSnake de Obijuan, en GitHub
#include <EEPROM.h>

Zowi zowi;

 int val; 
 int encoder0PinA = A2;
 int encoder0PinB = A3;
 int buttonPin = A0;
 int encoder0Pos = 0;
 int encoder0PinALast = LOW;
 int n = LOW;

int homePos[] = {90, 90, 90, 90};
int trims[4];
int tt = 0;
int buttonState = 0;         // current state of the button
int lastButtonState = HIGH;     // previous state of the button

void setup() { 
	memset(trims, sizeof(trims), 0);
 	
	zowi.init(2, 3, 4, 5, false);
 	zowi.setTrims(0,0,0,0);
 	zowi.home();
	zowi._moveServos(500,homePos);
    
    pinMode (encoder0PinA,INPUT);
   	pinMode (encoder0PinB,INPUT);
   	pinMode (buttonPin, INPUT_PULLUP);
   	for (int i=0; i< 3; i++)
   		showTrims(i);
   		
   	Serial.begin (9600);
 } 

void showTrims(int i)
{
   	Serial.print("Trim ");
   	Serial.print(i+1);
  	Serial.print(" is ");
   	Serial.println(trims[i]);
}

 void loop() { 

 	buttonState = digitalRead(buttonPin);
  	if (buttonState != lastButtonState) 
  	{
    	if (buttonState == HIGH) 
    	{
	    	showTrims(tt);
	      	tt++;
			if (tt > 3) tt = 0; 	  	
    	}
        delay(50);
  	}
  	lastButtonState = buttonState;
	
   	n = digitalRead(encoder0PinA);
   	if ((encoder0PinALast == LOW) && (n == HIGH)) {
    	if (digitalRead(encoder0PinB) == LOW) {
       		trims[tt]--;
     	} else {
       		trims[tt]++;
     	}
	
		zowi.setTrims(trims[0],trims[1],trims[2],trims[3]);
		zowi._moveServos(250,homePos);
		
     	Serial.print(tt+1);	
     	Serial.print(": ");
     	Serial.println (trims[tt]);
   	} 
   	encoder0PinALast = n;
 } 
